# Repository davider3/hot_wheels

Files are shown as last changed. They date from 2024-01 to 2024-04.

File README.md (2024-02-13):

# Notes

I will be keeping track of my progess and files on [GitHub](https://github.com/davider3/hot_wheels)

## Mechanical

### Car

I bought a 1996 Ferrari F50 hot wheels car that is 1:64th scale. I chose this car because I had the same one when I was a kid and it was my favorite one. It will make this project a bit harder due to how slim it is but it will look cooler so... worth it.

### Wheels

The plan is to 3D print the rims and then use a small O-ring as the tire.

### Steering

The mechanics of the steering is what I expect to be the hardest part on the mechanical side. I am going to need to do more research on this part.

## Electrical

### Microcontrollers

I have choosen to use the [Xiao ESP32S3](https://www.seeedstudio.com/XIAO-ESP32S3-Sense-p-5639.html) because it has built in wifi and BLE as well as a camera module all while being about the size of my thumb nail.
Because I don't want to solder headers on the the ESP32S3 I am using a [Xiao nRF52840](https://www.seeedstudio.com/Seeed-XIAO-BLE-nRF52840-p-5201.html) that I have on hand for some of the breadboard testing such as with the motors. It is very similar to the ESP32S3 both in how it's programmed and it's pinouts.

### Motors

#### DC Motors

I plan to use a DC motor to run the drive train of the car. I have 3 small dc motors that I am going to run some tests on to see if there is a clear winner. I will be using a DRV883 motor driver to drive the motor.

* *AliExpress Motor*
  * Starts to spin when pwm set to 130
  * Doesn't seem to get going very fast
* *DC Motor from Servo*
  * TODO
* *Drones Motor*
  * TODO

#### Servo Motor

A linear servo motor will be used to control the steering. [This](https://www.aliexpress.us/item/3256803902617918.html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) is the one that I have ordered and am waiting for its arrival for testing.

### Camera

I am usig the camera module that came with the ESP32S3.

### Wireless Comunication

#### Wifi

The ESP32S3 can host it's own site where it can stream the video that it is recording. I am expecting this to be one of the most difficult parts of this project because it is something that I have never attempting and do know much about. I also found a video that talks about how I can make the wifi connectivity dynamic instead of having to hard code the credentials in the code when I upload it. I will look more into that after I get the hard coding version working

#### Bluetooth

I have learned the the Xiao ESP32S3 can not use both BLE and wifi simultaneously so here are some possible options to get bluetooth working

* [nRF52832](https://www.adafruit.com/product/4077)
  * This one seems the most promising and I have ordered it
* [Adafruit](https://www.adafruit.com/product/2633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)
* [EMB1061](https://www.digikey.com/en/products/detail/seeed-technology-co.,-ltd/113990637/9991618?utm_adgroup=&utm_source=google&utm_medium=cpc&utm_campaign=PMax%20Shopping_Product_Medium%20ROAS%20Categories&utm_term=&utm_content=&utm_id=go_cmp-20223376311_adg-_ad-__dev-c_ext-_prd-9991618_sig-CjwKCAiA5L2tBhBTEiwAdSxJXz18duXnDFGFxcSPZGcyd4cDNltrNpTvqeeqjhoR4t047QVLTzL3cRoCpKkQAvD_BwE&gad_source=1&gclid=CjwKCAiA5L2tBhBTEiwAdSxJXz18duXnDFGFxcSPZGcyd4cDNltrNpTvqeeqjhoR4t047QVLTzL3cRoCpKkQAvD_BwE)

### Other

One of the other things that I want to include is some headlights
Something else that I have thought about is that I might need to get rid of the original base of the car and replace it with a custom pcb to make everything fit. But I will need to do some testing first.
I will be using a 3.7V Lipo battery that I can solder directly to the microcontroller. Both of the Xiao micros allow for charging of the battery through the usb-c port. The size of the battery will depend on the left over space in the car.

## Software

I will be using the Platformio extension of VS Code to do the programming. My plan is to have a sketch that can individually control each of the components before integrating them.

### Things to control with code

#### For the Car

* [x] Xiao nRF52840
* [x] Xiao ESP32S3
* [x] Motor and driver
* [x] Camera
* [x] Servo
* [ ] ~~Bluetooth Module~~
* [ ] Radio Module
* [ ] Battery and charging
* [ ] Headlights

#### For the Controller

* [x] nRF52840
* [x] Joystick
* [ ] ~~Bluetooth~~
* [ ] Radio Module
* [ ] Throttle Potentiometer
* [ ] SIM Steering wheel potentiometer 
* [ ] SIM Throttle potentiometer

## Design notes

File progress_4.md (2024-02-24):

# Progress Update 4

David Reinhardt

Relative to my original schedule I am staying right on track but some of my future milestones have changed because of some of the changes I have needed to make

## Success Criteria (in order of priority)

* [ ] Car can drive
* [ ] Car can turn
* [ ] Car is controlled by a wireless controller
* [ ] FPV video stream works
* [ ] Racing sim setup
* [ ] Car will have headlights

## Mechanical

I have done a lot of research and design work for the front suspension and have ordered all of the parts to begin making it. The same material that I ordered for it will be used for the drive train.

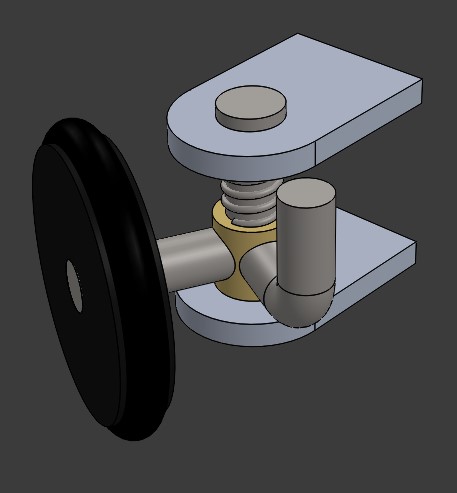
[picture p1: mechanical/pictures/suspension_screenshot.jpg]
sus


I have also been test fitting everything into the car and been grinding down the parts of the car that I won't need. I am feeling pretty confident about fitting everything inside even though it is such a small car. It will be one of the most difficult parts of this project though

yikes

## Electrical

I created a full electrical schematic and have started soldering some of the components to the main microcontroller.

## Software

I have interfaced with all of the components that I currently have but am still waiting for the radio controller to arrive. That will be a difficult part of this as well

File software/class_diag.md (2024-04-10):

# Class Diagram

```mermaid
---
title : RC HotWheels
---
classDiagram

    class Car{
        -Motor motor
        -s3servo steer
        -Comms radio
        -int headlights
        +Car(int mtrPin1, int mtrPin2, int servoPin)
        +void drive()
    }
  
    Car --|> Motor : Has
    Car --|> Comms : Has

    class Motor{
        -int goPin
        -int backPin
        -int enPin
        +Motor(int go, int back, int en=-1)
        +void forward(int val)
        +void backward(int val)
        +void powerOn(bool turnOn)
    }

    class Comms{
        -char dir
        -char throttle[3]
        -char steering[3]
        -char lights
        -int i

        +Comms()

        +void checkComm()

        +int getThrottle()
        +int getSteeing()
        +int getLights()
        +int getDir()
    }

    note "Camera.h
    IPAddress camSetup(const char* ssid, const char* password)"

```

```mermaid
---
title : RC Controller
---
classDiagram

    class Controller{
        -int throttle
        -int steer
        -int lights
        -int dir
        -int throttleBias
        -int steerBias
        -int i
        -Comms radio
        -void throttleCalc()
        -void steerCalc()
        -void calibrate()

        +Controller()
        +void control()

    }
  
    Controller --|> Comms : Has

    class Comms{
        +Comms()
        +void sendSignal()
    }

```

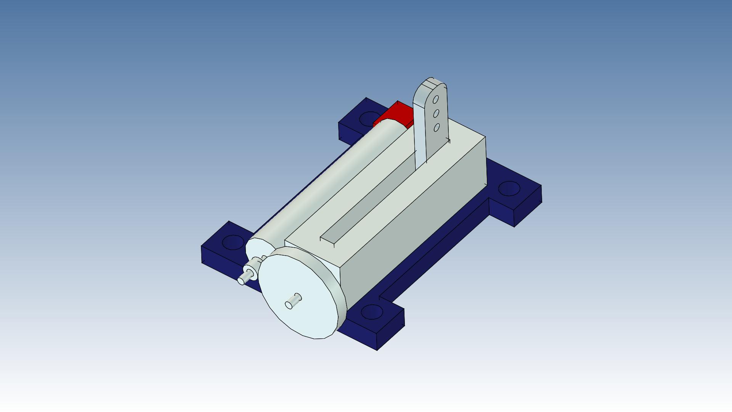
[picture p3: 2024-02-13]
mechanical/pictures/micro linear servo.jpg

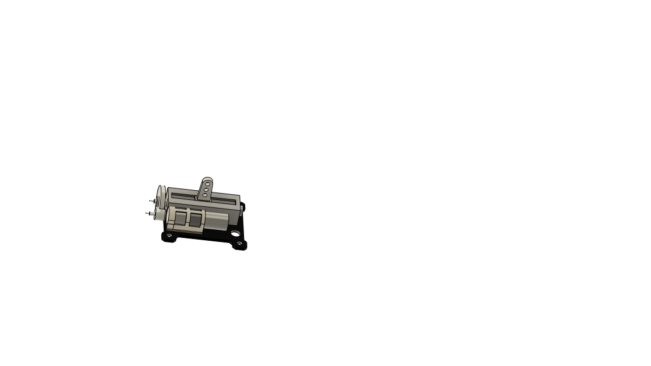
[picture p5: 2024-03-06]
mechanical/pictures/Flash Hobby Micro Analog 1.png

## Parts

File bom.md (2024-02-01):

# Update 3

David Reinhardt

## Bill of Materials

### Car

| Item | Quantity| Ordered | Working |
| --- | --- | --- | --- |
|Xiao ESP32S3 | 1 | X | X |
|Camera| 1 | X | X |
|DRV8833 Motor Driver | 1 | X | X |
| DC Motor | 1 | X | - |
| Car | 1 | X | - |
| Linear servo | 1 | X | -|
|Surface mount LED | 2 | - | -|
|nRF52832 BLE | 1 | X | -|
| O-rings for tires | 4 | X | -|
|Steering Mechanism| 1 | -| - |

### Controller

| Item | Quantity| Ordered | Working |
| --- | --- | --- | --- |
|ESP32| 1 | X | X |
|Joystick| 1 | X | - |
|Potentiometers| 3 | - | - |

## Milestones

- Week 4(this week) - Get camera working, order all parts
- Week 5 - Make motor selection, Create model of car and all components, full electrical schematic
- Week 6 - Design suspension, interface with servo, test together
- Week 7 - Build hand held controller Controller
- Week 8 - Get bluetooth module working with camera simultaneously
- Week 9 - Full circuit/code testing
- Week 10 - Fit all components in 3D Model
- Week 11 - Full Car assembly
- Week 12 - Testing and debuging
- Week 13 - Build racing sim setup

## Testing/Prototypes

- I have been testing which of 3 small dc motors that I have will be the best but so far have only tested one of them.
- I have already gotten the camera on the Xiao ESP32S3 to stream to a local server that it is hosting which I expected to be much more difficult but I got it first try
- I have been doing a lot of ordering of the different components this week and the majority are on their way, the rest I will have ordered by this saturday
- I was able to successfully remove the base of the hot wheels ferrari with out destroying it which is something else I was slightly worried about

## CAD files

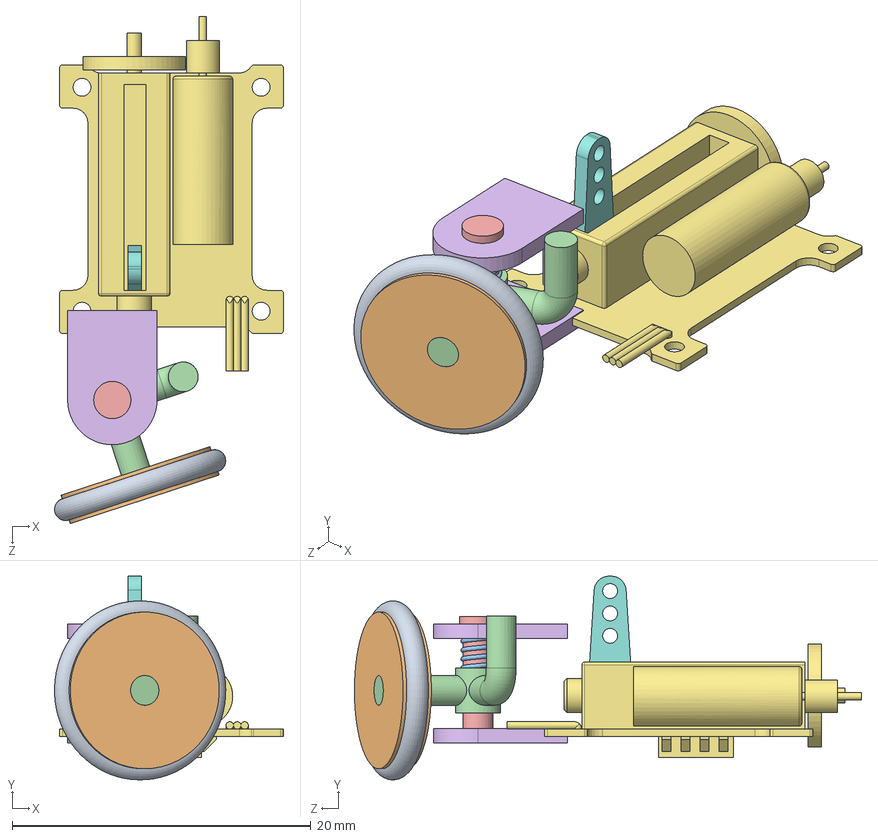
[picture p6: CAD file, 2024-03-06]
mechanical/servo.SLDASM
15.3 x 13.6 x 34.0 mm
servo_arm
servo_body
control_arm x 2
front_shock
upright
spring
rim
o_ring

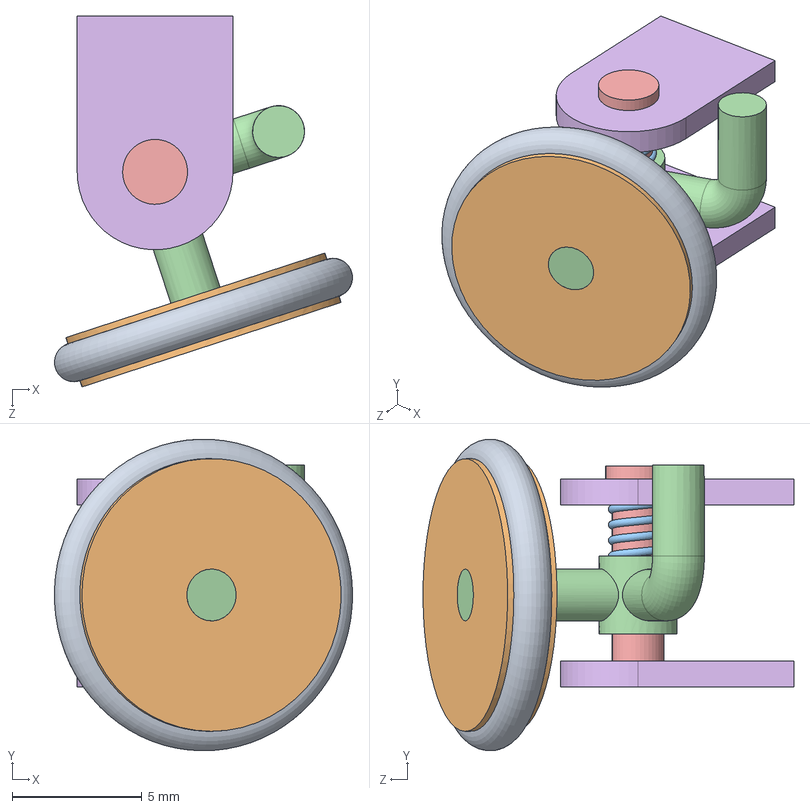
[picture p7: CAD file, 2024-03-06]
mechanical/front_suspension.SLDASM
11.5 x 12.0 x 14.3 mm
control_arm x 2
front_shock
upright
spring
rim
o_ring

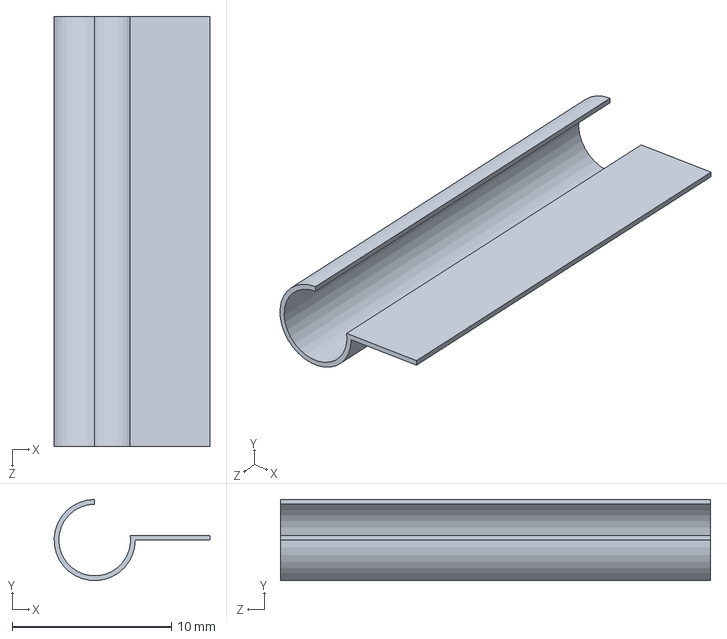
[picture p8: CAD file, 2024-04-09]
mechanical/motor_mount.SLDPRT
9.77 x 5.09 x 27.0 mm

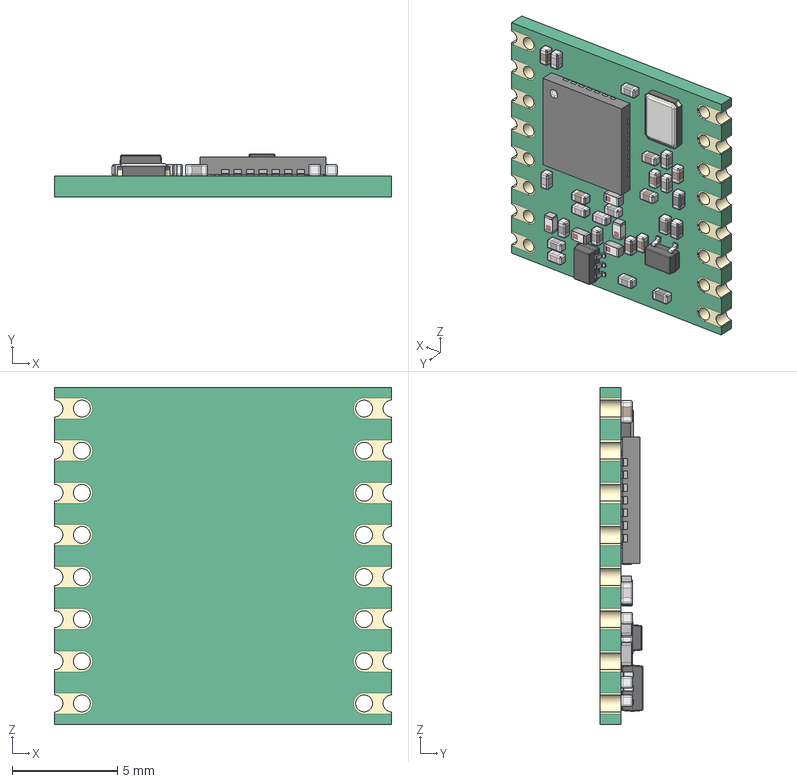
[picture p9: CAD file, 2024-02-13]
mechanical/other_files/RFM95 LoRa v15.step
16.0 x 2.04 x 16.0 mm
QFN 28
SMD Crystal
CAP 0403 x 8
CAP Ceramic 0403 x 8
Res 0403 x 4
CAP ML 0403 x 5
SOT-323
Inductor SMD 0403 x 5
SOT-363

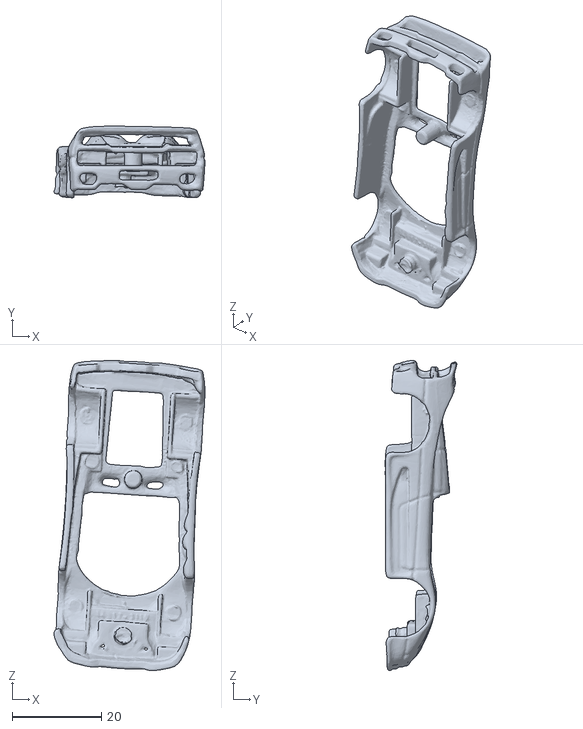
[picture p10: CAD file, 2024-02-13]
mechanical/other_files/ferrari.stl
33.9 x 16.1 x 69.6

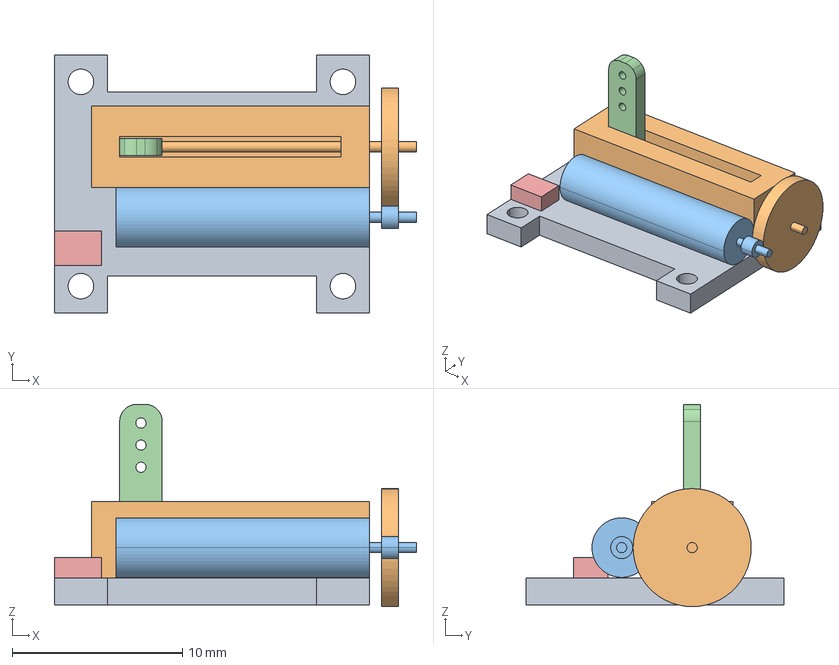
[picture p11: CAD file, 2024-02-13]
mechanical/other_files/micro linear servo.stp
21.3 x 15.1 x 11.9 mm

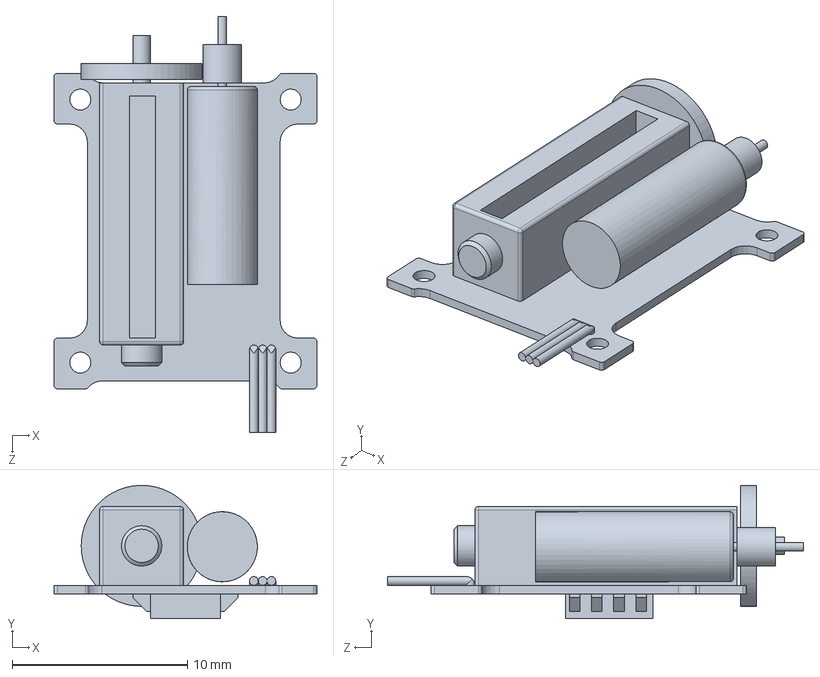
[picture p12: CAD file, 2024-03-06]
mechanical/servo_body.SLDPRT
15.0 x 7.60 x 23.8 mm

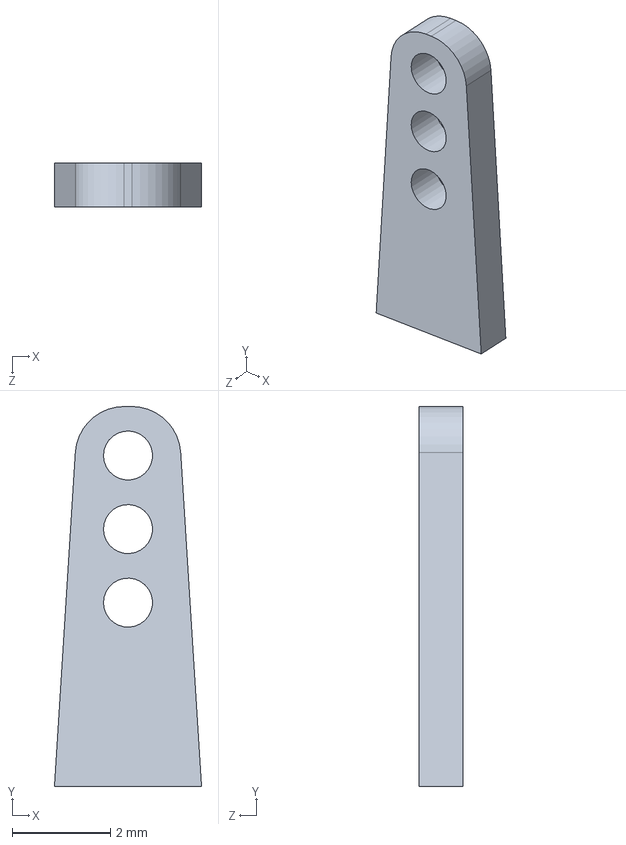
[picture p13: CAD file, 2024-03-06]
mechanical/servo_arm.SLDPRT
3.00 x 7.75 x 0.9 mm

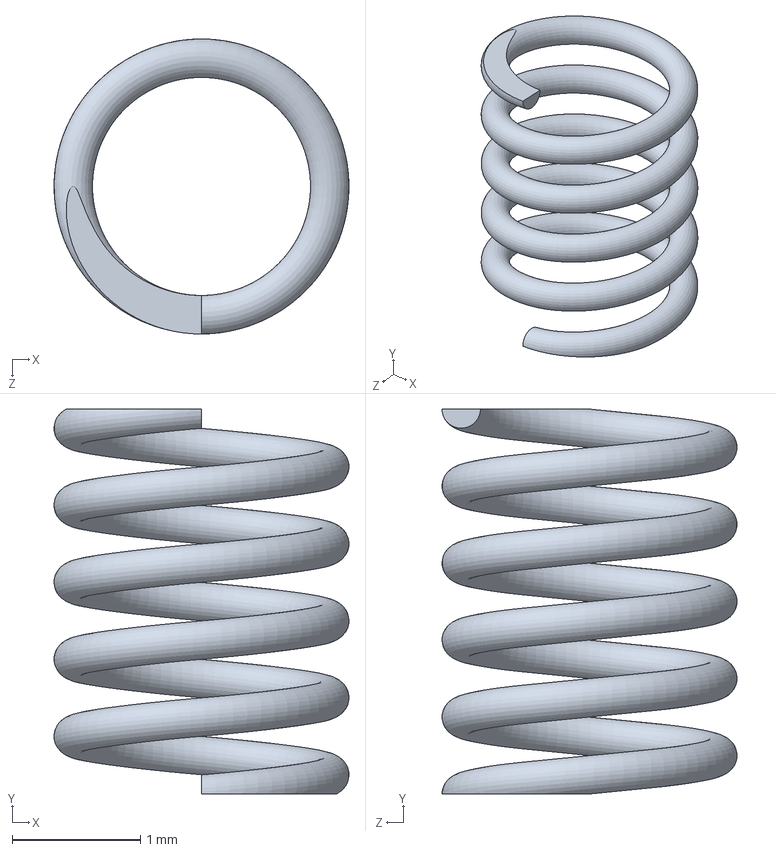
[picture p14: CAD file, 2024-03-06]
mechanical/spring.SLDPRT
2.30 x 3.00 x 2.30 mm

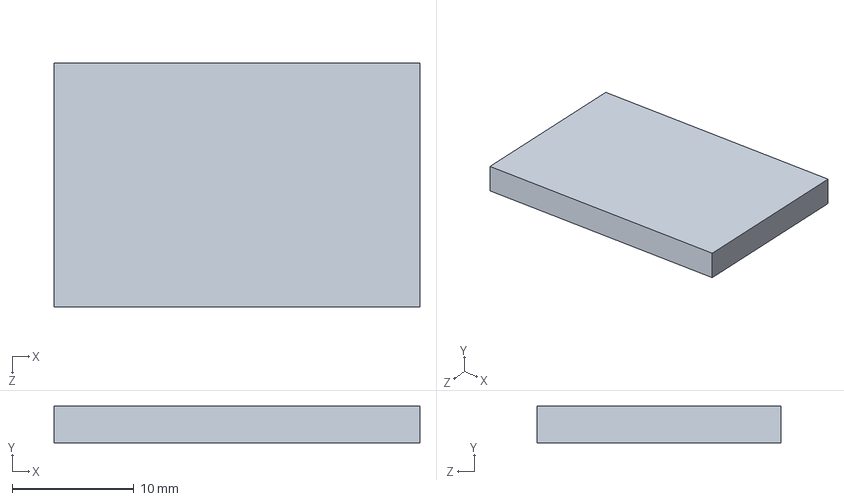
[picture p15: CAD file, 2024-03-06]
mechanical/battery.SLDPRT
30.0 x 3.00 x 20.0 mm

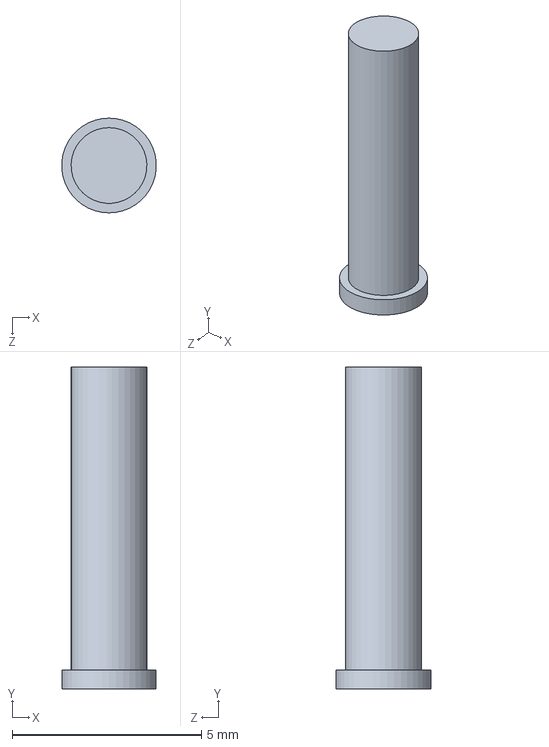
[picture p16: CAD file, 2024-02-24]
mechanical/front_shock.SLDPRT
2.49 x 8.50 x 2.50 mm

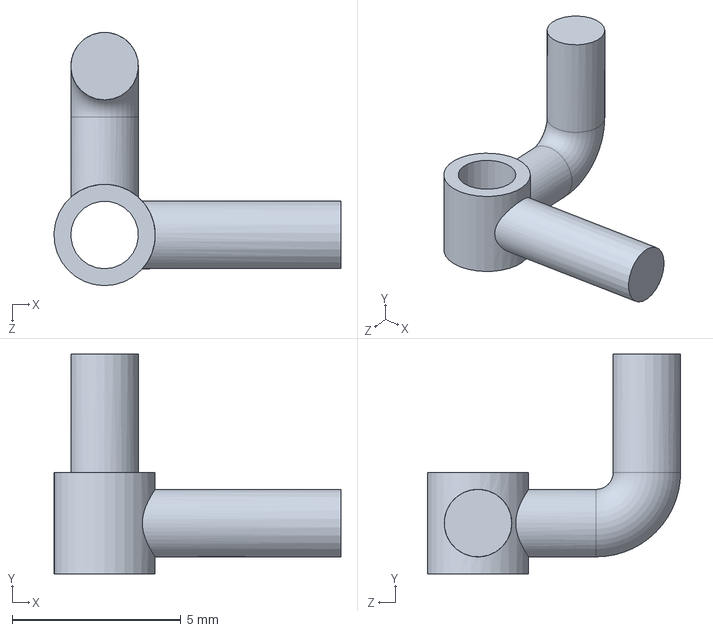
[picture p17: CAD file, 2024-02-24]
mechanical/upright.SLDPRT
8.50 x 6.50 x 7.50 mm

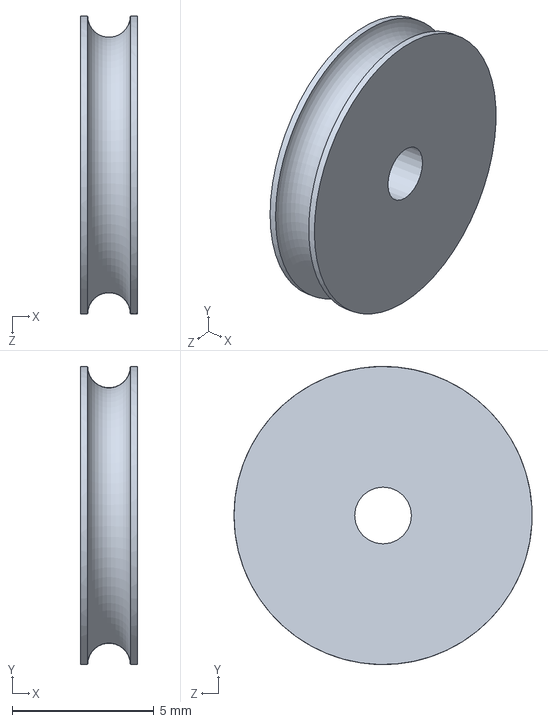
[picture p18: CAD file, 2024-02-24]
mechanical/rim.SLDPRT
2.00 x 10.5 x 10.5 mm

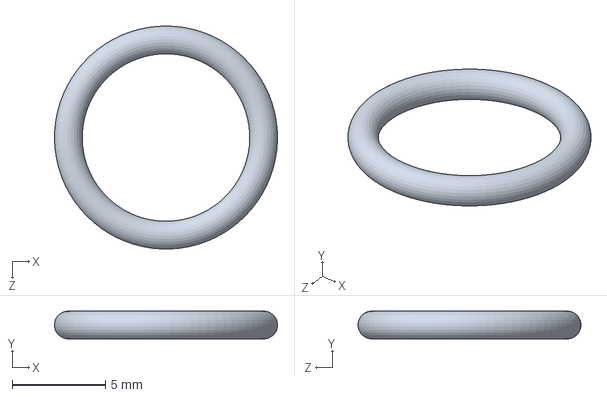
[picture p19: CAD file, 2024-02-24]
mechanical/o_ring.SLDPRT
12.0 x 1.50 x 12.0 mm

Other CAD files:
mechanical/rfm95w.SLDASM
mechanical/control_arm.SLDPRT
mechanical/DRV8833.SLDPRT
mechanical/dc_motor.SLDPRT
mechanical/motor_mount.STL
mechanical/other_files/micro linear servo.stl

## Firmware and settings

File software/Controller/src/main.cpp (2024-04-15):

/* 
 * Project to be uploaded to a RC controller
 * Created By David Reinhardt
 */

#include <Arduino.h>
#include <SPI.h>
#include <LoRa.h>
#include "params.h"
#include "Controller.h"

Controller control;

void setup() {

    Serial.begin(9600);

    pinMode(LED_BUILTIN, OUTPUT);
    digitalWrite(LED_BUILTIN, LOW);

    control = Controller();
    digitalWrite(LED_BUILTIN, HIGH);
}

void loop() {
    control.control();
    delay(50);
}

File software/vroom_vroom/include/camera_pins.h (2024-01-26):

#if defined(CAMERA_MODEL_XIAO_ESP32S3)

#define PWDN_GPIO_NUM     -1
#define RESET_GPIO_NUM    -1
#define XCLK_GPIO_NUM     10
#define SIOD_GPIO_NUM     40
#define SIOC_GPIO_NUM     39

#define Y9_GPIO_NUM       48
#define Y8_GPIO_NUM       11
#define Y7_GPIO_NUM       12
#define Y6_GPIO_NUM       14
#define Y5_GPIO_NUM       16
#define Y4_GPIO_NUM       18
#define Y3_GPIO_NUM       17
#define Y2_GPIO_NUM       15
#define VSYNC_GPIO_NUM    38
#define HREF_GPIO_NUM     47
#define PCLK_GPIO_NUM     13

#else
#error "Camera model not selected"
#endif

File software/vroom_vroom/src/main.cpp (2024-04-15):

/* 
 * Project to be uploaded to a RC FPV HotWheels Car
 * Created By David Reinhardt
 */

#include <Arduino.h>
#include "Camera.h"
#include "Car.h"
#include "params.h"

IPAddress ip;
Car car;

// WIFI
// const char* ssid = "David";
// const char* password = "ckmh013$";
const char* ssid = "Helm's Depot";
const char* password = "sweetballoon047";

void setup() {
    Serial.begin(115200);
    Serial.setDebugOutput(true);

    delay(5000);
    Serial.println();
    Serial.println("Begin");

    // ip = camSetup(ssid, password);
    // Serial.println("Cam setup");
    
    car = Car();
    // car.sendIP(ip);
    Serial.println(ip);
}

void loop() {

    car.drive();
    car.printDebug();
    // Serial.println(ip);
    delay(100);
}

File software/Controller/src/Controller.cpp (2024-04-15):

#include "Controller.h"

Controller::Controller(){
    pinMode(JOYSTICK, INPUT);
    pinMode(TRIGGER, INPUT); 
    pinMode(LIGHTS, INPUT);
    throttle = 0;
    steer = 90;
    lights = 0;
    dir = 1;

    calibrate();

    radio = Comms();

    // // TEST
    // while(radio.checkComm());
    // screen.showIP(radio.getIPAddress());

}

void Controller::calibrate(){
    throttleBias = 0;
    steerBias = 0;

    for(i = 0; i < 10; ++i){
        throttleBias += analogRead(TRIGGER);
        steerBias += analogRead(JOYSTICK);
    }

    steerBias = steerBias / 10;
    throttleBias = throttleBias / 10;
}

void Controller::control(){
    throttleCalc();
    steerCalc();
    lights = digitalRead(LIGHTS);

    Serial.print("Throttle: ");
    Serial.print(throttle);
    Serial.print(dir ? " forward " : " backward ");
    Serial.print("Turn: ");
    Serial.print(steer);
    Serial.print(" Lights are ");
    Serial.println(lights ? "on" : "off");

    radio.sendSignal(dir, throttle, steer, lights);
}

void Controller::throttleCalc(){
    throttle = analogRead(TRIGGER);

    if(throttle > throttleBias - 20 && throttle < throttleBias + 20){
        dir = 1;
        throttle = 0;
    } else if(throttle < throttleBias){
        dir = 0;
        // TODO: increase 0 to whatever value starts to spin the motors
        throttle = map(throttle, throttleBias, 0, 0, 255);
    } else if(throttle > throttleBias){
        dir = 1;
        // TODO: increase 0 to whatever value starts to spin the motors
        throttle = map(throttle, throttleBias, 4095, 0, 255);
    }else{
        dir = 1;
        throttle = 0;
    }
}

void Controller::steerCalc(){
    steer = analogRead(JOYSTICK);

    if(steer < steerBias){
        steer = map(steer, 0, steerBias, 0, 90);
    }else{
        steer = map(steer, steerBias, 4095, 90, 180);
    }
}

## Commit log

2024-01-23 blinked LED
2024-01-23 motor spins
2024-01-24 ready to test camera
2024-01-26 antenna math
2024-01-30 camera done
2024-02-06 motor driver model
    [DRV8833.IGS, DRV8833.SLDPRT, DRV8833.STEP]
2024-02-13 created servo test
2024-02-13 schematic first draft
    [ki_cad.kicad_sch]
2024-02-13 3D model progress
    [DRV8833.IGS, DRV8833.SLDPRT, DRV8833.STEP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]
2024-02-13 servo works
2024-02-22 Suspension Progress
    [control_arm.SLDPRT, front_shock.SLDPRT, front_suspension.SLDASM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]
2024-03-20 camera working
2024-04-09 motor mount testing
    [motor_mount.SLDPRT, motor_mount.STL]
2024-04-09 added reset and nss pins
    [ki_cad.kicad_sch]
2024-04-09 controller works
    [motor_mount.SLDPRT, motor_mount.STL]
2024-04-10 updated schematic
    [ki_cad.kicad_sch]
2024-04-10 fixed servo issue and upload issues
    [main.cpp, params.h]
2024-04-15 esp32s3 connects to rfm98 and parses data correctly
    [Car.cpp, Controller.cpp, main.cpp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]
